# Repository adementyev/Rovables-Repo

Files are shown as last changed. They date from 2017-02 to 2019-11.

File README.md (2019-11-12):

# Rovables Project 

## Introduction
This repository has all the design files to assemble the robots. Rovables are miniature wearable robots that can move around the body. 
See the paper we published at UIST conference [here](http://www.artemdementyev.com/wp-content/uploads/2016/10/Rovables-Miniature-On-Body-Robots-as-Mobile-Wearables.pdf).  

Rovables rendered
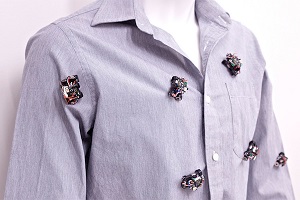
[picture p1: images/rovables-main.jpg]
Shirt pic


## Content
electronics/ - contains the circuit boards design. They were all designed using Altium, so it might be required to see the original files

mechanical/ - This folder contains mechanical files, done in SolidWorks 2016. 

software/ - contains the software that runs on the devices. We used the Arduino platform, so the robots can be easily programmed.  

## Manufacturing and design
The design contains many 3D printed custom parts and custom circuit boards. Making the design will require at least a good resolution 3D printer (Formlabs or Eden260). Other printers might work also, but we haven't tried them. 

## Known Issues
The same nRF42 library is used for the robot and the receiver. Change in nRF52.cpp file: #define TEENSY_MASTER_BOARD depending on which one, since they use different SPI port definitions. 

The localization of the robot is not implemented in the current code. This version has high resolution wheel encoders and a powerful ARM processor, so the tracking will be better. 

## Aknowledgements
This project was a collaboration between MIT Media Lab (Responsive Environments and Living Mobile) and Shape Lab at Stanford University

The poeple who worked on this project are:

Graduate students: Artem Dementyev, Hsin-Liu (Cindy) Kao, Inrak Choi, Deborah Ajilo, Maggie Xu. 

The faculty: Sean Follmer, Joe Paradiso, Chris Schmandt.

Undegraduate students: Lucas Santana, Karla-Sofia Zapata-Garcia, Cheyenne Hua, and Diana Lamaute

Shapelab Logo
MediaLab Logo

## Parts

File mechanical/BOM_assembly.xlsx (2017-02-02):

Part | Quantity | Supplier | Comments
Off Shelf
M2 7mm standoffs | 2 | Amazon (https://www.amazon.com/gp/product/B00W94LVRG/ref=oh_aui_detailpage_o06_s00?ie=UTF8&psc=1)
M2 4mm standoffs | 2 | Amazon (https://www.amazon.com/gp/product/B00R1IWHZU/ref=oh_aui_detailpage_o02_s00?ie=UTF8&psc=1)
M2 3mm screw | 6 | Amazon (https://www.amazon.com/gp/product/B00QFS2X2O/ref=oh_aui_detailpage_o00_s02?ie=UTF8&psc=1)
M1.6 3mm screw | 2 | Amazon (https://www.amazon.com/gp/product/B00QFSLIUM/ref=oh_aui_detailpage_o06_s00?ie=UTF8&psc=1)
M1.6 nut | 2 | Amazon (https://www.amazon.com/gp/product/B01LWZ5UXQ/ref=oh_aui_detailpage_o05_s00?ie=UTF8&psc=1)
Magnets | 4 | K&J Magnetics (https://www.kjmagnetics.com/search-pn.asp?pg=1&stext=R621) | 3/8'' x 1/8 '' x 1/16''
Thicker magnets | 2 | K&J Magnetics (https://www.kjmagnetics.com/proddetail.asp?prod=R622) | 3/8'' x 1/8'' x 1/8''
100mAh battery | 1 | Amazon (https://www.amazon.com/gp/product/B00IHA4W1S/ref=oh_aui_detailpage_o00_s00?ie=UTF8&psc=1)
4x8x3mm bearings | 2 | Amazon (https://www.amazon.com/gp/product/B019I2WVCA/ref=oh_aui_detailpage_o06_s00?ie=UTF8&psc=1)
Custom PCBs
Main control board | 1 | PCB cart (http://www.pcbcart.com/pcb-fab/pcb-prototype.html) | They can do 0.5mm 4-layer board
IR encoder boards | 2 | PCB cart (http://www.pcbcart.com/pcb-fab/pcb-prototype.html) | The board has to be routed correctly
Encoder disks | 2 | PCB cart (http://www.pcbcart.com/pcb-fab/pcb-prototype.html) | 0.5mm thick
Flex cables | 2 | King Credie (http://www.kingcredie.com/)
Programming shield | 1 | OSH park (https://oshpark.com/)
3D Printed
Main body | 1 | Formlabs | GPBK02 Resin, 25um resolution
undercarriage | 1 | Formlabs | GPBK02 Resin, 25um resolution
Ball bearing adapter | 2 | Formlabs | GPBK02 Resin, 25um resolution
Motor adapter | 2 | Formlabs | GPBK02 Resin, 25um resolution
Cover | 1 | Formlabs | GPBK02 Resin, 25um resolution
Rod for magnets | 1 | Formlabs | GPBK02 Resin, 25um resolution
Tools needed
#0 Phillips screwdriver | 1
Form 2 Printer | 1 |  | Eden260 is ok also
Solder iron | 1

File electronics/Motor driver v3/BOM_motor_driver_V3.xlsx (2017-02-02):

Comment | Description | Designator | Footprint | Quantity | Manufacturer 1 | Manufacturer Part Number 1 | Supplier 1 | Supplier Part Number 1
ON_OFF_SWITCH | SPDT SMD Side Switch | *1 | SWTICH_SMD_SIDE | 1 | Nidec / COPAL ELECTRONICS | CUS-12TB | Digi-Key | 563-1102-1-ND
2.4GHz SMT On-ground MID Chip Antenna | Bluetooth antenna | A1 | 47948-0001 | 1 | Molex | 479480001 | Digi-Key | WM4893CT-ND
2.45 GHz Bulan | for nRF8001 chip | B1 | 2450BM14A0002 | 1 | Johanson Technology | 2450BM14A0002T | Digi-Key | 712-1574-1-ND
100uF 6.3V | Polarised capacitor | C1 | CAP1206 | 1 | Vishay / Sprague | TL8A0107M6R3C | Digikey | 718-1920-1-ND
10uF 16V | Polarised capacitor | C2 | CAP0805 | 1 | Kyocera / AVX | F981C106MSA | Digi-Key | 478-8654-1-ND
10uF 6.3V | Polarised capacitor | C3 | 0805 TANTALUM | 1 | Kyocera / AVX | TPSR106K006R1000 | Digi-Key | 478-9265-1-ND
0.1uF | SMD Cap 1206 | C5, C12 | 0603W | 2 | Yageo | CC0603ZRY5V9BB104 | Digikey | 311-1343-1-ND
0.1uF | SMD Cap 1206 | C6, C10, C17, C18 | 0402 CAPACITOR | 4 | Samsung | CL05A104MP5NNNC | Digikey | 490-1318-1-ND
18pF | SMD Cap 1206 | C8, C9 | 0402 CAPACITOR | 2 | Murata | GRM1555C1H180JA01D | Digikey | 490-5858-1-ND
33nF X7R, +/- 10% | SMD Cap 1206 | C11 | 0402 CAPACITOR | 1 | Kemet | C0402C333K4RACTU | Digikey | 399-4891-1-ND
6pF NPO, +/- 2% | SMD Cap 1206 | C14, C15 | 0402 CAPACITOR | 2 | Murata | GRM1555C1H6R0WA01D | Digikey | 490-8223-1-ND
2200pF 5% | SMD Cap 1206 | C16, C19 | 0402 CAPACITOR | 2 | Kemet | C0402C222J3GACTU | Digikey | 399-8957-1-ND
10000pF | SMD Cap 1206 | C20 | 0402 CAPACITOR | 1 | Murata | GRM155R71H103KA88D | Digikey | 490-4516-1-ND
10uF 16V | SMD Cap 1206 | C22 | 0603W | 1 | Murata (https://octopart-clicks.com/click/altium?sku=81-GRM188C81C106MA3D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) | GRM188R60G106ME47D (https://octopart-clicks.com/click/altium?sku=81-GRM188C81C106MA3D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) | Digikey | 490-3298-1-ND (https://octopart-clicks.com/click/altium?sku=81-GRM188C81C106MA3D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)
4.7uF 10V | SMD Cap 1206 | C23 | 0603W | 1 | Murata | GRM188R61A475KE15D | Digikey | 490-10477-1-ND
Ferrite bead |  | L1 | 0603W | 1 | Murata | BLM18PG471SN1D | Digikey | 490-5223-1-ND
LED BLUE | LED SMD 1206/0603 | LED1 | 0402W | 1 | Panasonic / Panasonic SSG | LNJ947W8CRA | Digi-Key | LNJ947W8CRACT-ND
LED RED | LED SMD 1206/0603 | LED2 | 0402W | 1 | Panasonic / Panasonic SSG | LNJ247W82RA | Digi-Key | LNJ247W82RACT-ND
LED ORANGE | LED SMD 1206/0603 | LED3 | 0402W | 1 | Panasonic / Panasonic SSG | LNJ437W84RA | Digi-Key | LNJ437W84RACT-ND
32.768 kHz |  | O1 | 32.768 Crystal | 1 | ECS International | ECS-.327-12.5-34B-TR | Digi-Key | XC1617CT-ND
16 MHz Crystal Cl=8pF | For BLE use | O2 | 2.5 x 2.0 crystal | 1 | Nihon Dempa Kogyo (NDK) | NX2520SA-16MHZ-STD-CSW-5 | Digi-Key | 644-1169-1-ND
FH33J-4S-0.5SH(99) | 0.5mm FPC connector | P3, P5, P6 | FH33J-4S-0.5SH(99) | 3 | Hirose Electric (HRS) | FH33J-4S-0.5SH(99) | Digi-Key | H124646CT-ND
CONN HEADER 20POS |  | P4 | DF12 20 POS | 1 | Hirose Electric (HRS) | DF12D(4.0)-20DP-0.5V(81) | Digi-Key | H11743CT-ND
10K |  | R2 | 0402 RESISTOR | 1 | Yageo | RC0402JR-0710KL | Digikey | 311-10KJRCT-ND
0 Ohm |  | R3, R4, R5 | 0402 RESISTOR | 3 | Yageo | RC0603JR-070RL | Digikey | 311-0.0GRCT-ND
22K 1% |  | R6 | 0402 RESISTOR | 1 | Yageo | RC0402FR-0722KL | Digikey | 311-22.0KLRCT-ND
330 |  | R7, R8 | 0402 RESISTOR | 2 | Yageo | RC0402JR-07330RL | Digikey | 311-330JRCT-ND
49.9K |  | R10, R13 | 0603W | 2 | Yageo | RC0603FR-0749K9L | Digikey | 311-49.9KHRCT-ND
20K |  | R11, R14 | 0603W | 2 | Yageo | RC0603FR-0720KL | Digikey | 311-20.0KHRCT-ND
200K |  | R12, R15 | 0603W | 2 | Yageo | RC0603FR-07200KL | Digikey | 311-200KHRCT-ND
4.7K 5% |  | R16, R17 | 0402 RESISTOR | 2 | Yageo | RC0402JR-074K7L | Digikey | 311-4.7KJRCT-ND
4.99K 1% |  | R18 | 0603W | 1 | Panasonic / Panasonic ECG | ERJ-3EKF4991V | Digikey | P4.99KHCT-ND
1K 5% |  | R20 | 0603W | 1 | Yageo | RC0603JR-071KL | Digikey | 311-1.0KGRCT-ND
3.3V REG | 5V LDO SMD | U1 | SOT-23-5 | 1 | Microchip Technology (https://octopart-clicks.com/click/altium?manufacturer=Microchip%20%2F%20Micrel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) | MIC5219-5.0YM5-TR (https://octopart-clicks.com/click/altium?manufacturer=Microchip%20%2F%20Micrel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) | Digi-Key | 576-1281-1-ND
3.3 V REG | 5V LDO SMD | U2 | SOT-23-5 | 1 | Microchip Technology (https://octopart-clicks.com/click/altium?manufacturer=Microchip%20Technology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) | MIC5205-3.3YM5-TR (https://octopart-clicks.com/click/altium?manufacturer=Microchip%20Technology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) | Digi-Key | 576-1259-1-ND (https://octopart-clicks.com/click/altium?manufacturer=Microchip%20Technology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)
MCP73831T |  | U4 | SOT-23-5 | 1 | Microchip Technology | MCP73831T-2ACI/OT | Digi-Key | MCP73831T-2ACI/OTCT-ND
nRF24L01+ | 2.4 GHz Radio | U6 | QFN20 | 1 | Nordic Semiconductor | nRF24L01P-R7 | Digi-Key | 1490-1033-1-ND
DRV8835 |  | U8 | WSON-16 | 1 | Texas Instruments (TI) | DRV8835DSSR | Digi-Key | 296-30391-1-ND
MPU 6050 | Gyro / accelerometer combo | U9 | QFN24 | 1 | Invensense | MPU-6050 | Digi-Key | 1428-1007-1-ND
MCP6422 | 4.4 µA/Amplifier, 90 kHz Op Amp | U10 | MSOP-MS8_N | 1 | Microchip Technology | MCP6422-E/MS | Digi-Key | MCP6422-E/MS-ND
ATSAMD21G | IC MCU 32BIT 256KB FLASH 48TQFP | U*1 | TQFN48 | 1 | Atmel | ATSAMD21G18A-AUT | Digi-Key | ATSAMD21G18A-AUTCT-ND

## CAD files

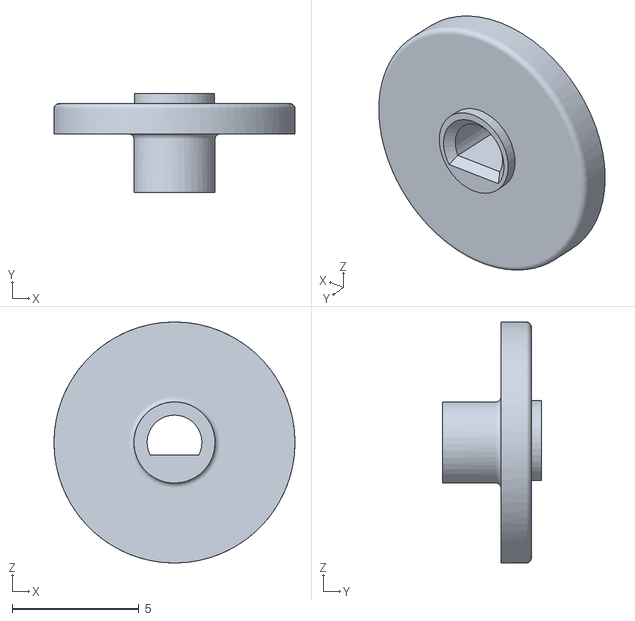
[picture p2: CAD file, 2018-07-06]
mechanical/CAD Robot/Rovables_assembly_magnetic_v5_for_3D_print/Mt_Mg Adapter V2.STL
9.50 x 3.90 x 9.50

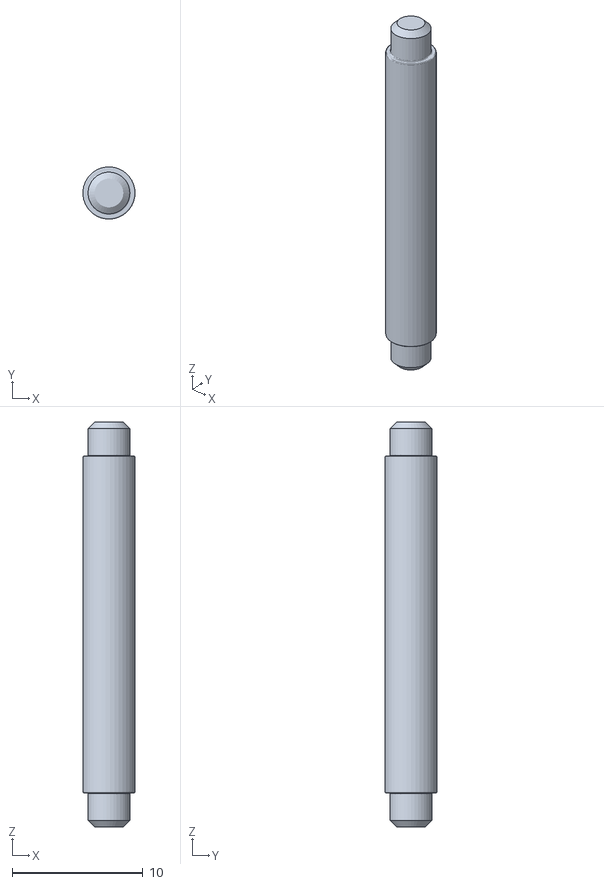
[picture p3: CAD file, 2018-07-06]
mechanical/CAD Robot/Rovables_assembly_magnetic_v5_for_3D_print/Magnet Holder V1C.STL
3.99 x 4.00 x 31.0

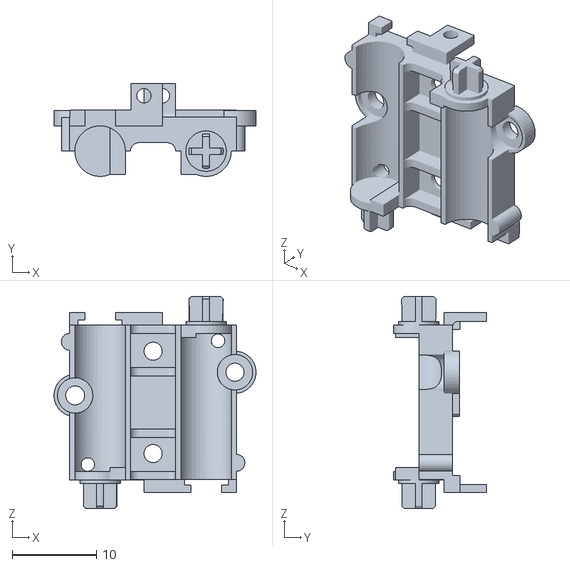
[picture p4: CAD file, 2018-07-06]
mechanical/CAD Robot/Rovables_assembly_magnetic_v5_for_3D_print/base_plate_v1.STL
23.9 x 11.0 x 25.2

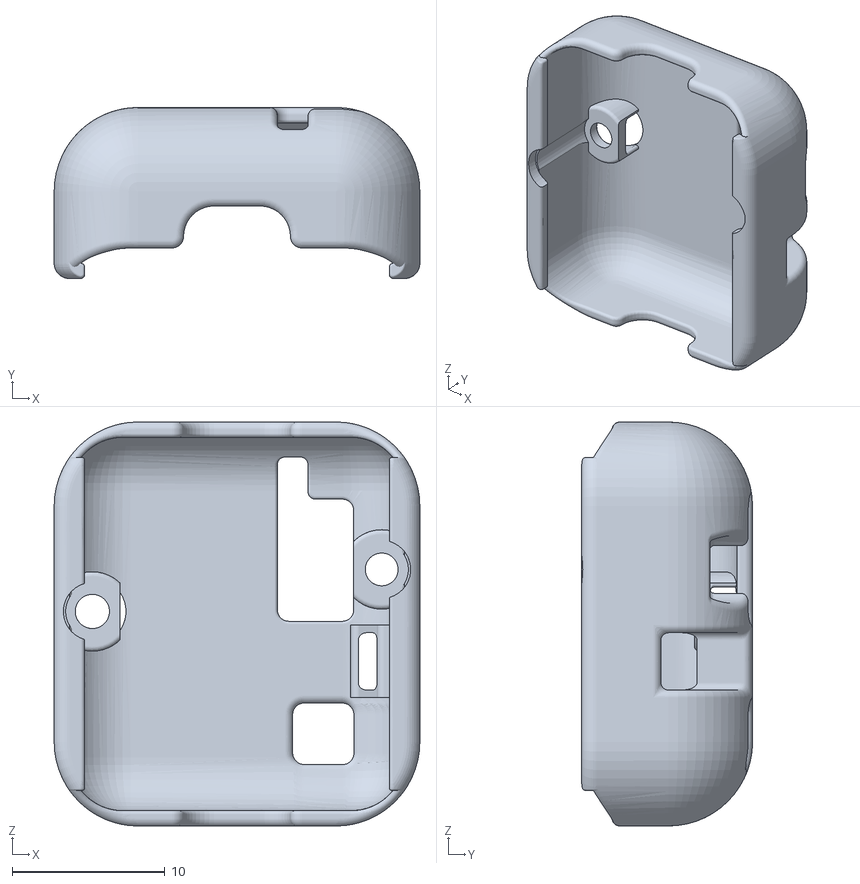
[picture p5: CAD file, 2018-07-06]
mechanical/CAD Robot/Rovables_assembly_magnetic_v5_for_3D_print/case_minimum_covered.STL
24.0 x 11.2 x 26.5

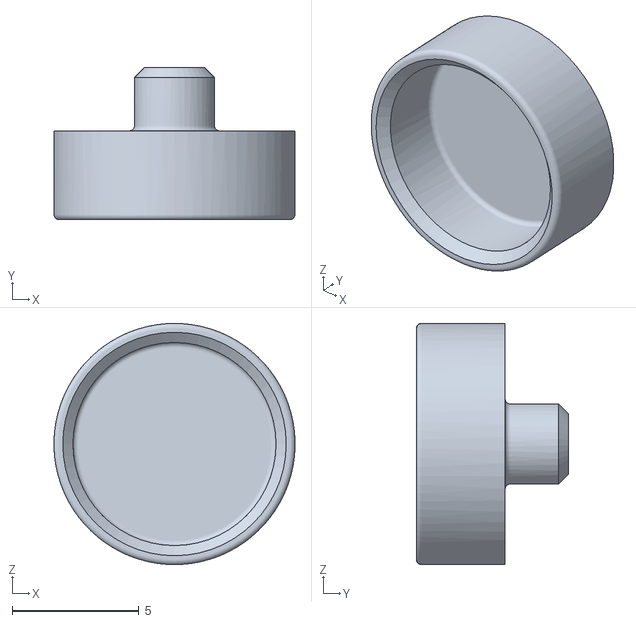
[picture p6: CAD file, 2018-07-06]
mechanical/CAD Robot/Rovables_assembly_magnetic_v5_for_3D_print/BB_Mg Adapter V2.STL
9.49 x 6.00 x 9.50

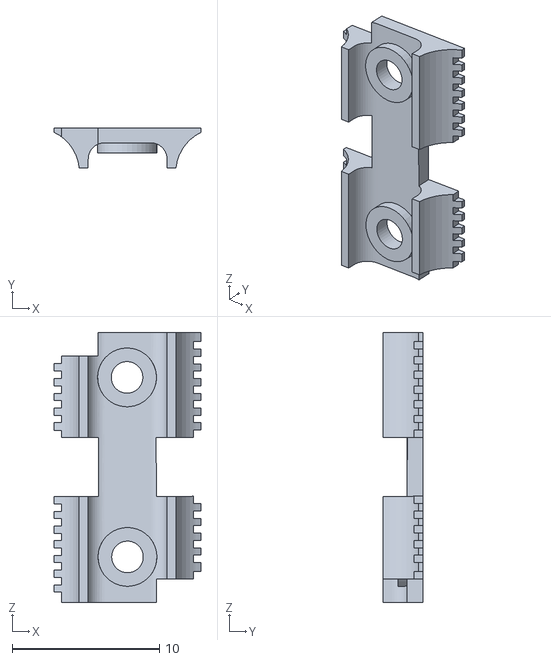
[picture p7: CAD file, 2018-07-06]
mechanical/CAD Robot/Rovables_assembly_magnetic_v5_for_3D_print/bottom_ski_v1.STL
9.99 x 2.70 x 18.4

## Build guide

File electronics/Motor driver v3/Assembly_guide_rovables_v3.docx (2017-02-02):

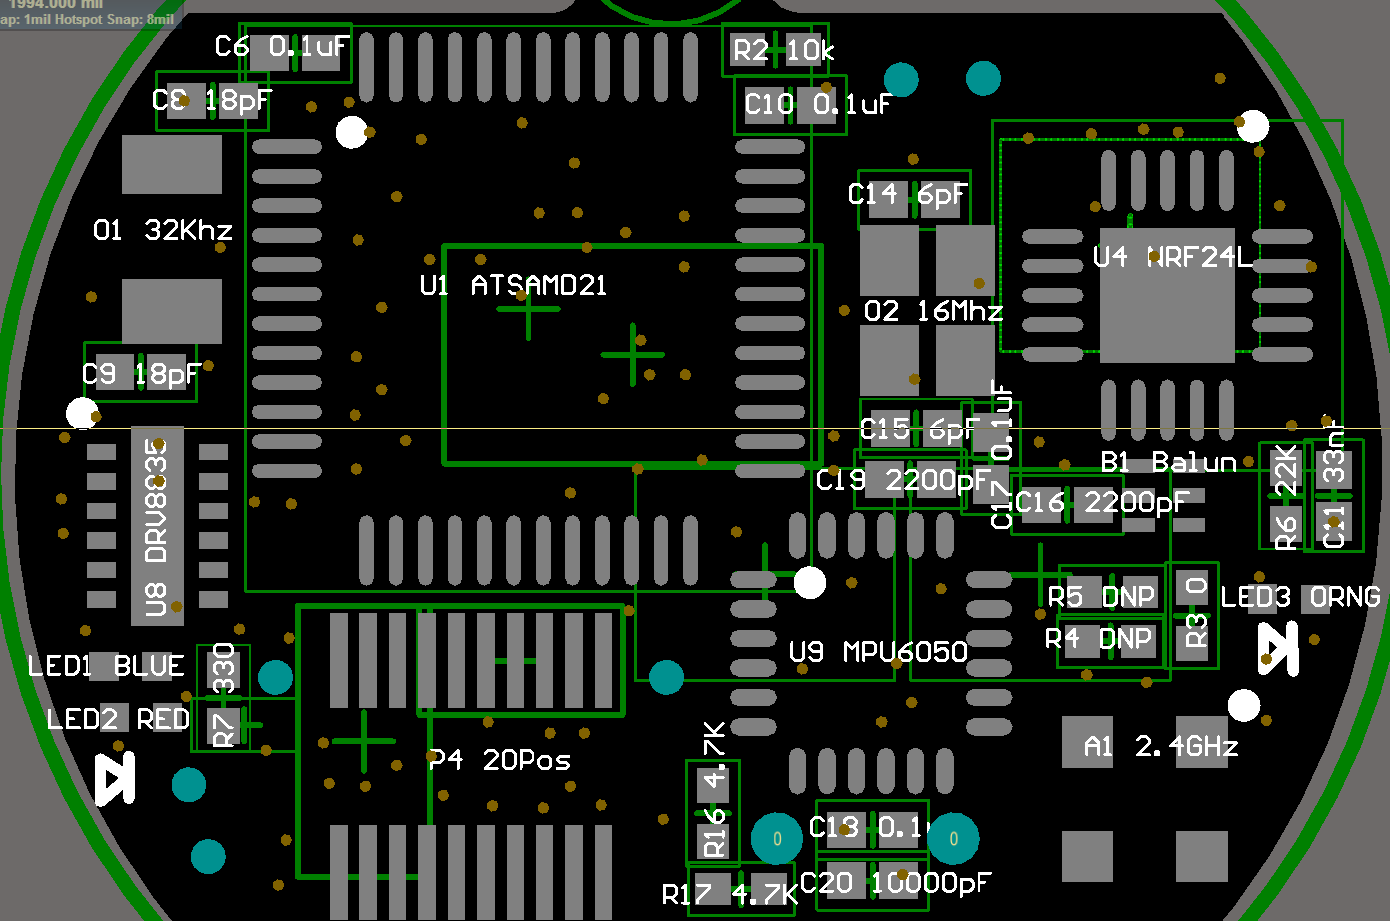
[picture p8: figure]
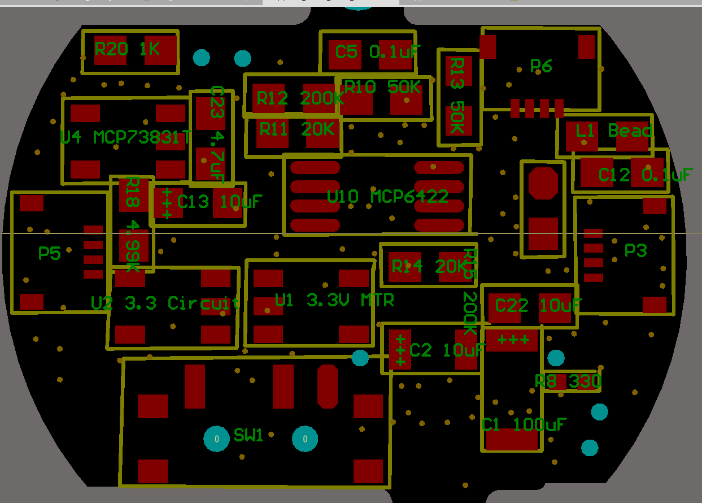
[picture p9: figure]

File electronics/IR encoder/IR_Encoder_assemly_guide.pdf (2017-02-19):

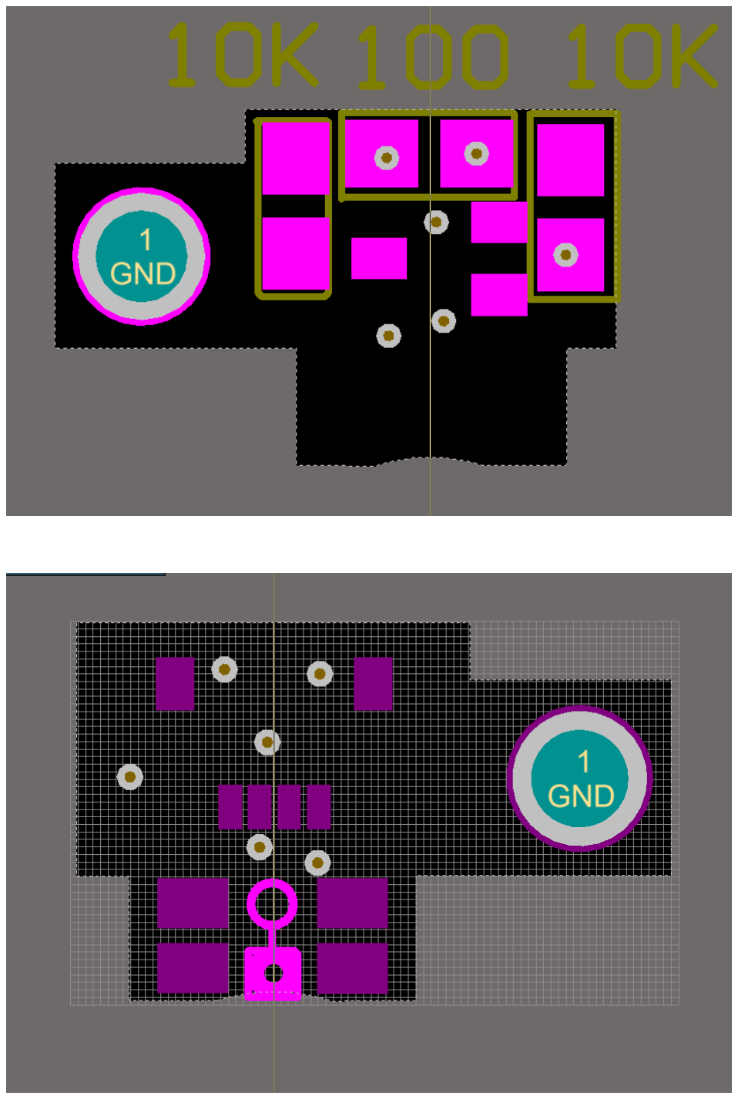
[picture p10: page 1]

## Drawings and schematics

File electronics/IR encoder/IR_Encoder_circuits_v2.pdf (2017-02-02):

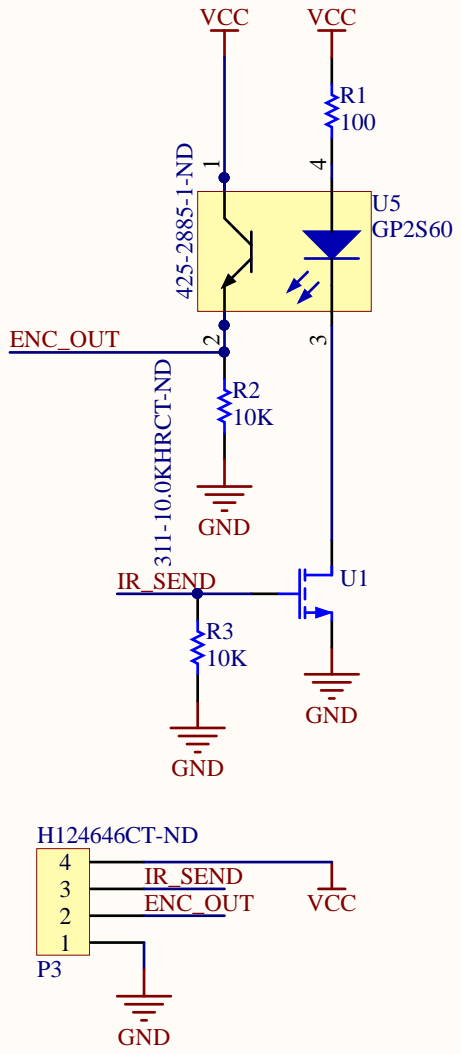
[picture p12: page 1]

IR Encoder Board Title

Designed by Artem Dementyev | 2 Ver

Date: 2/2/2017 Time: 2:40:27 PM

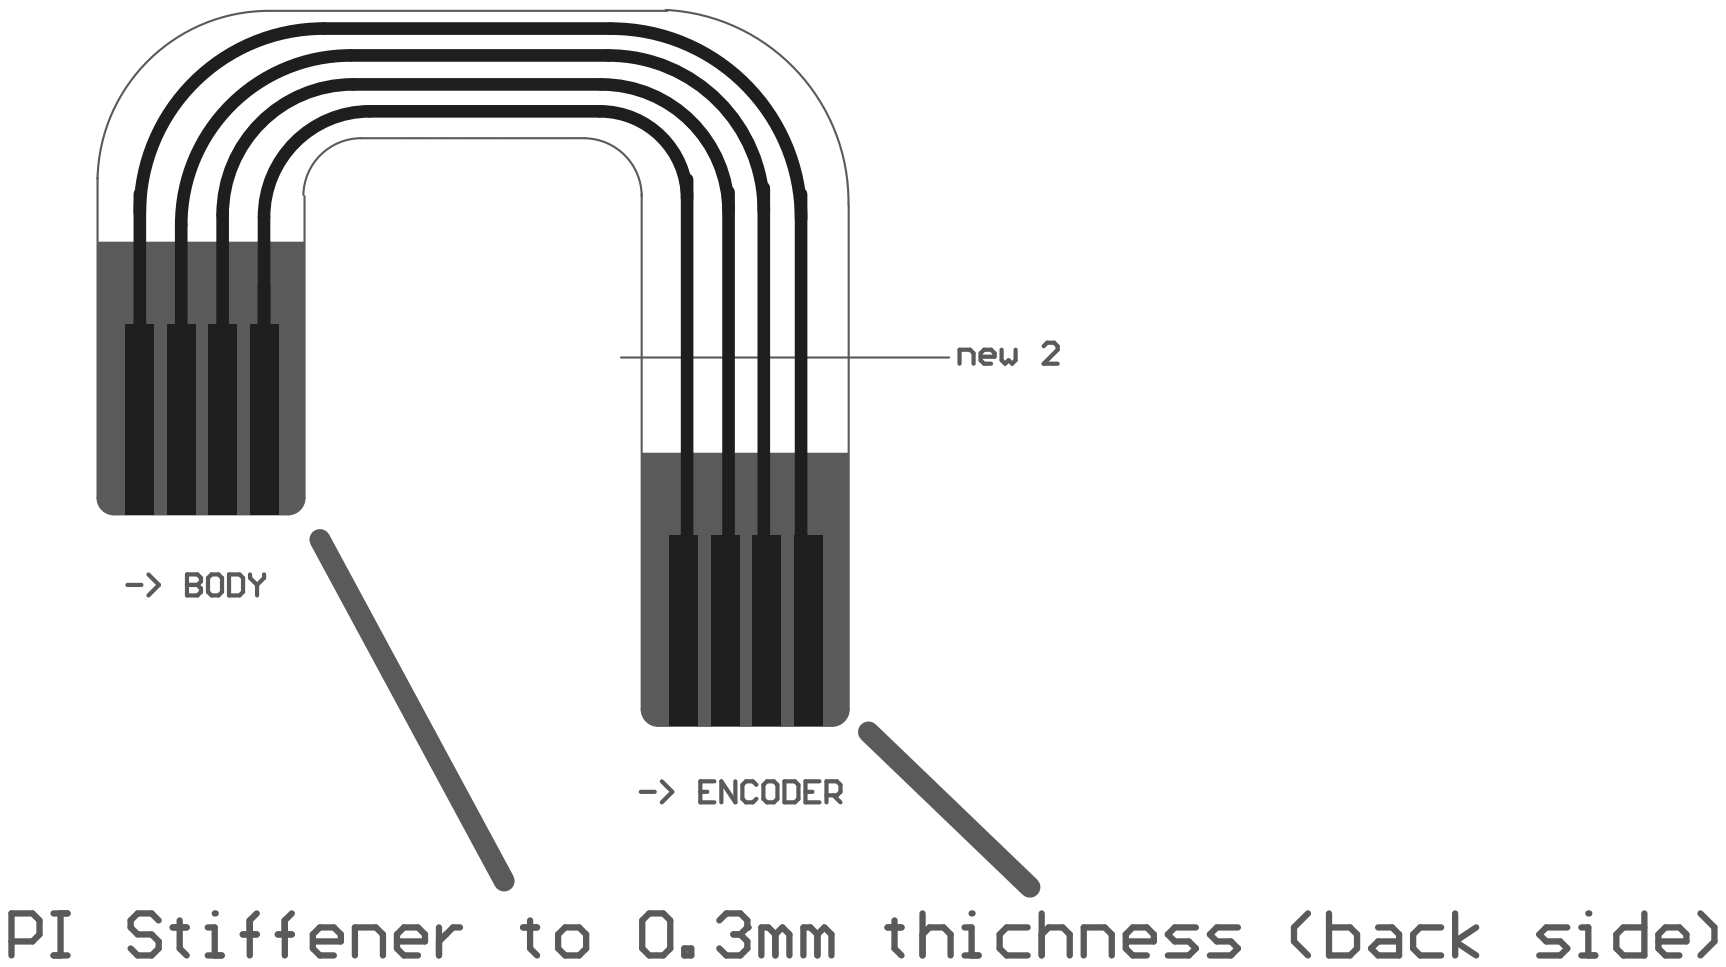
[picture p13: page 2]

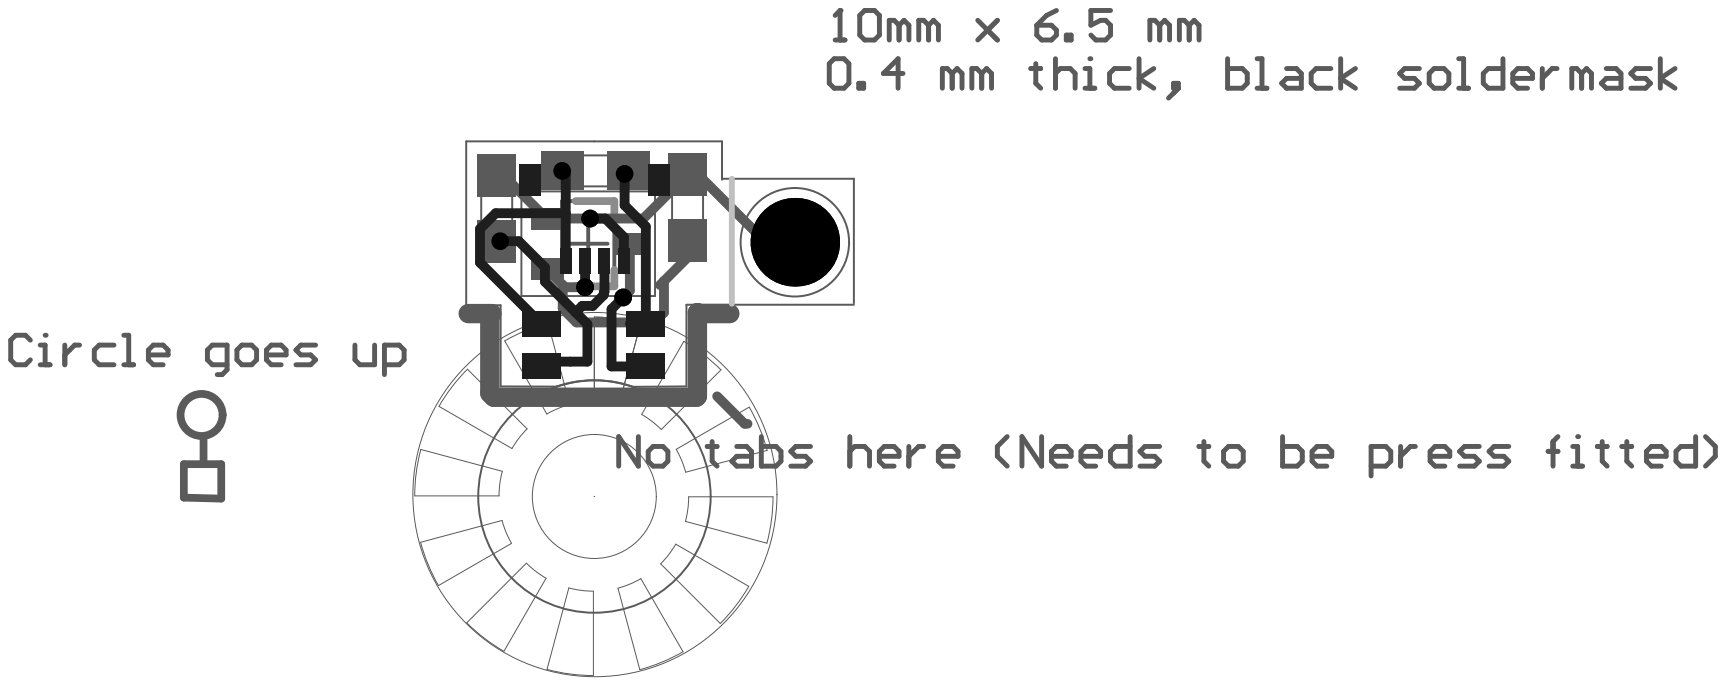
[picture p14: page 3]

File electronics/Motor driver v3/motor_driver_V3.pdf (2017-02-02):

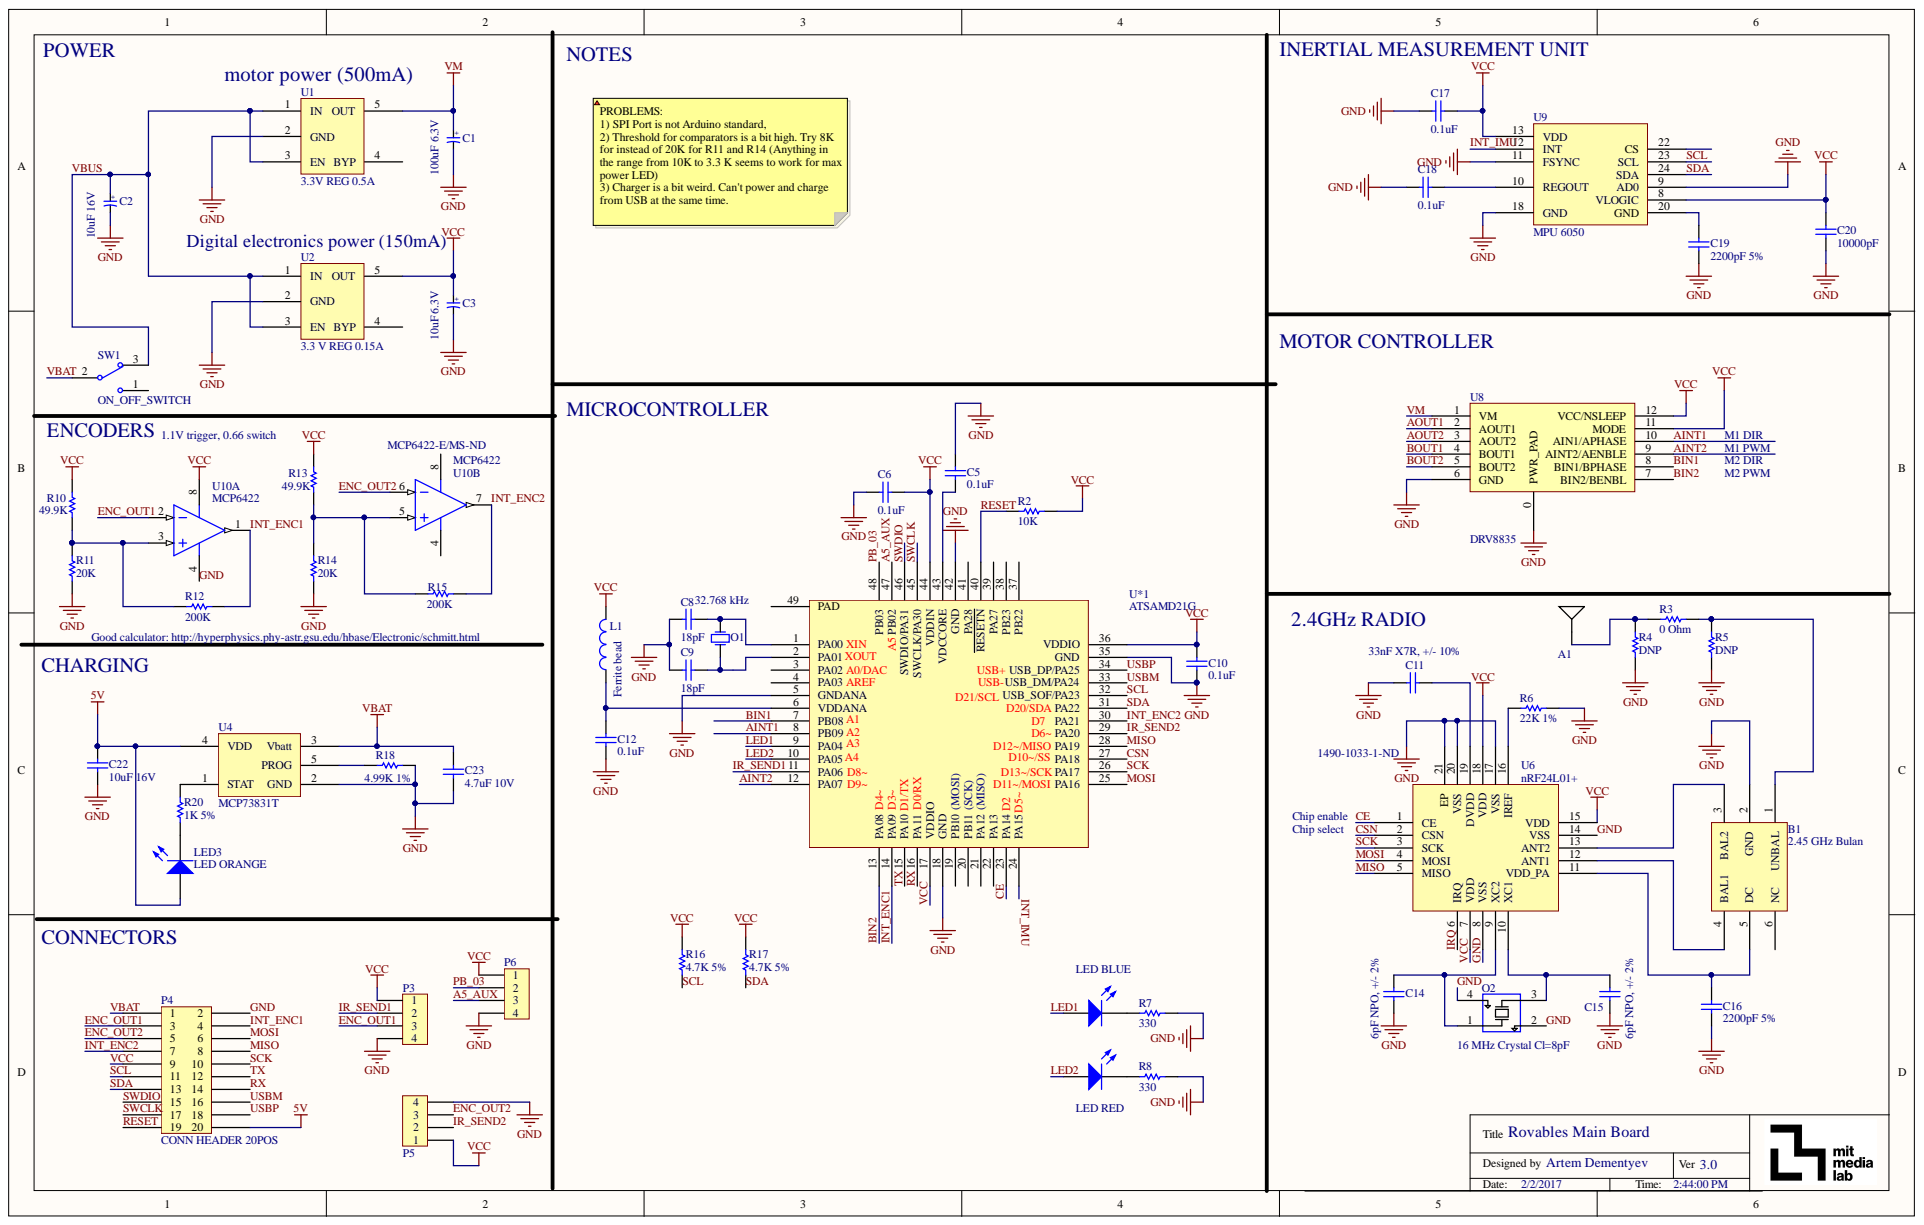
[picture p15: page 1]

tead of 20K for R
the range from 10K to 3.3 K seem
power L

Anything in
s to work for max

3) Charger i
from USB at the same t

tr.gsu.edu/hbase/E

IREF 16 VSS 17 VDD 18 DVDD 19 VSS 20 V

Des igned by A r tem Demen t yev | 3 . 0 Ver

Date: 2/2/2017 | Ti me: 2:44:00 PM

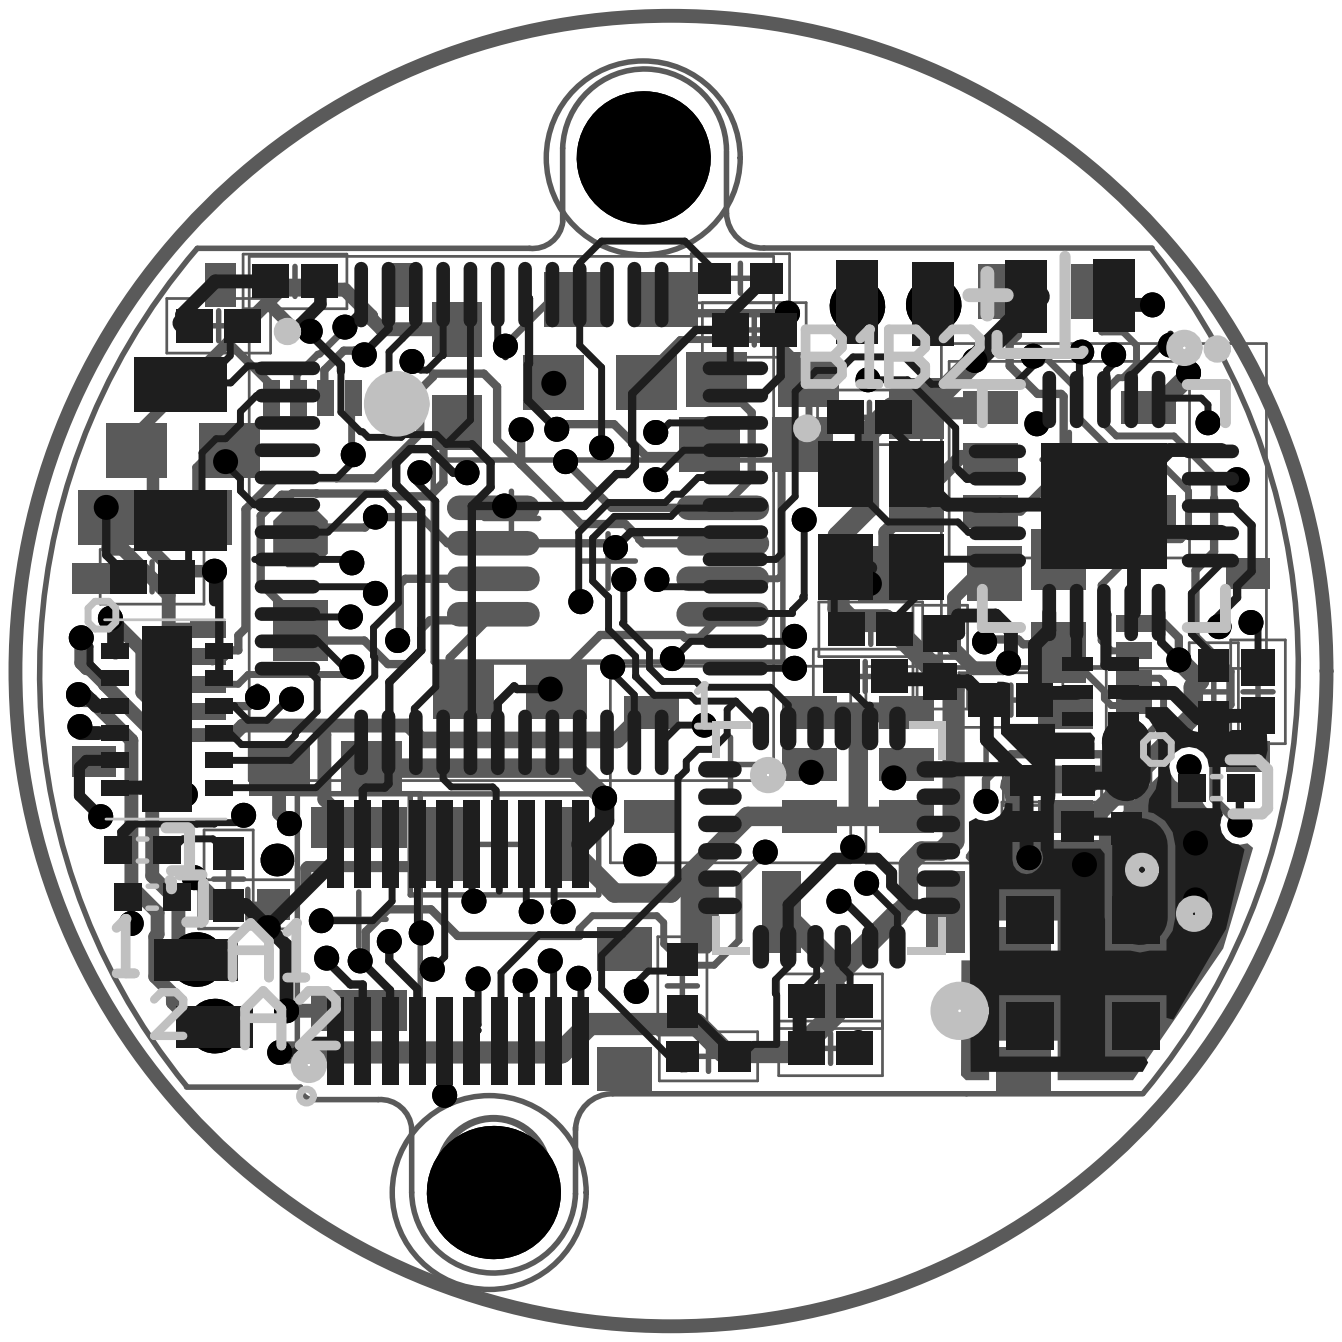
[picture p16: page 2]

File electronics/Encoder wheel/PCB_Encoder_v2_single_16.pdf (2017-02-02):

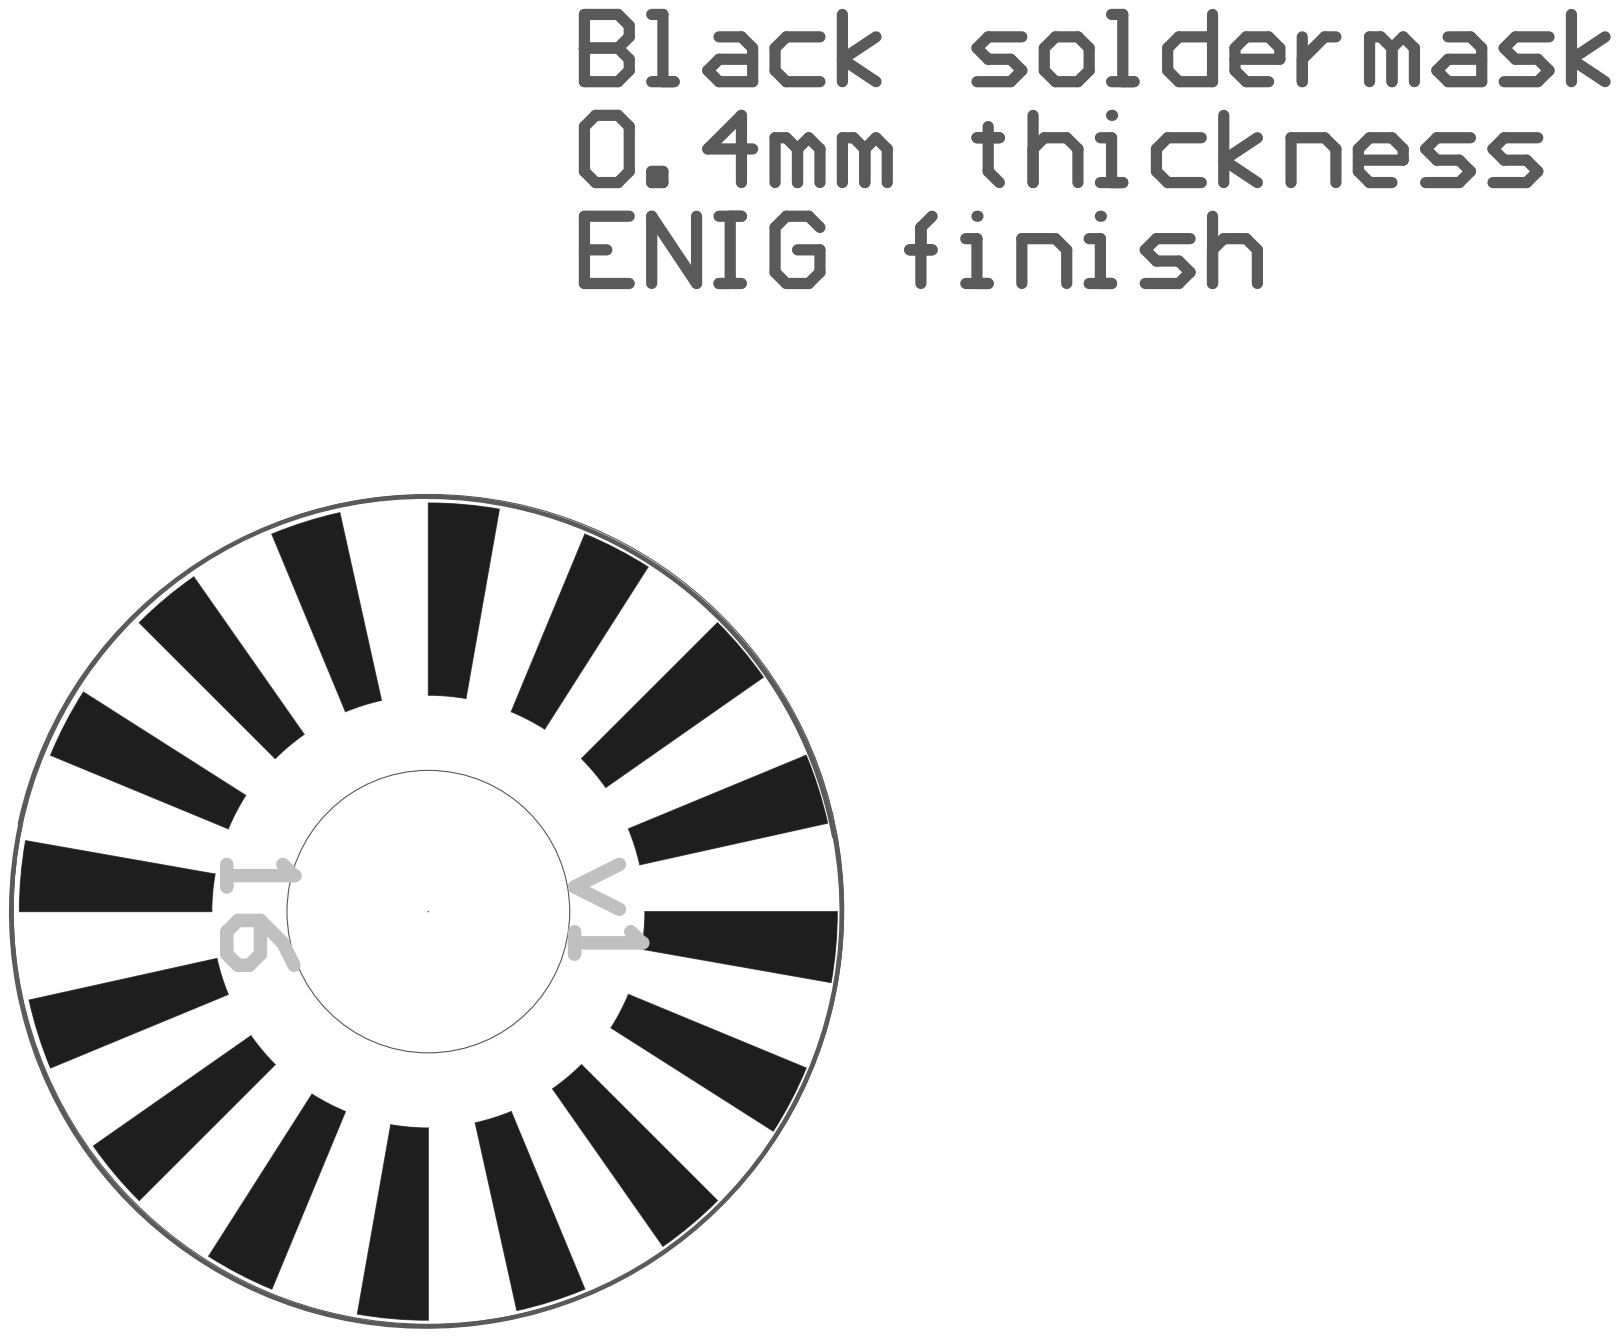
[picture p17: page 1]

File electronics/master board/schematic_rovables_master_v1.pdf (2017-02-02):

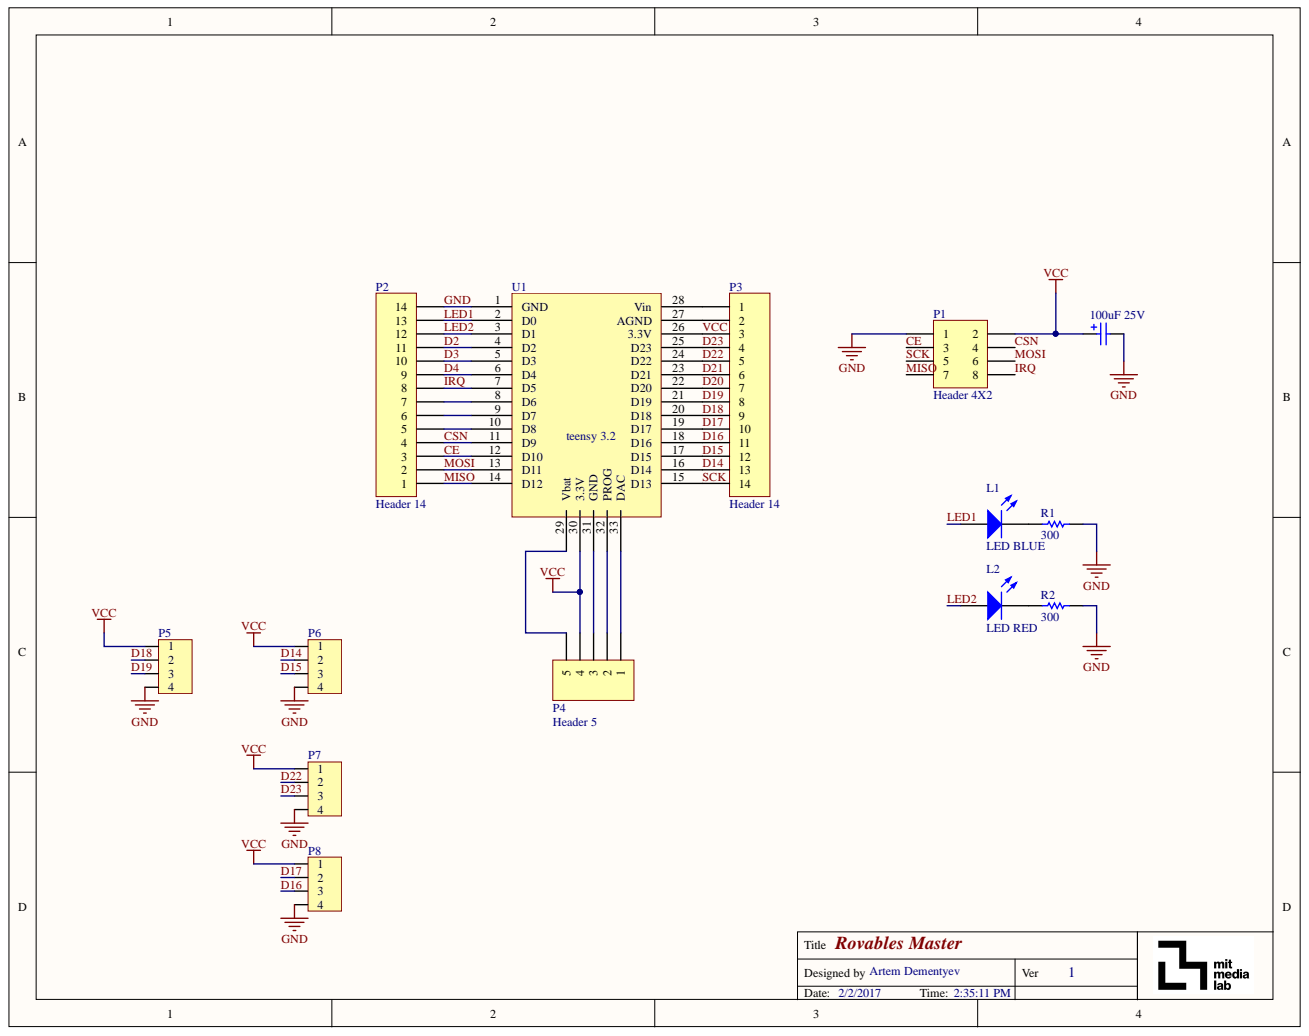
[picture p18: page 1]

D4 | D4 6 | D21
IRQ | D5 7 | D20

D6 8 | D19
D7 9 | D18
D8 10 | D17

CSN | D9 11 | D16
CE | D10 12 | D15
MOSI | D11 13 | D14
MISO | | SCK

Rovables Master Title

Designed by Artem Dementyev | 1 Ver

Date: 2/2/2017 Time: 2:35:11 PM

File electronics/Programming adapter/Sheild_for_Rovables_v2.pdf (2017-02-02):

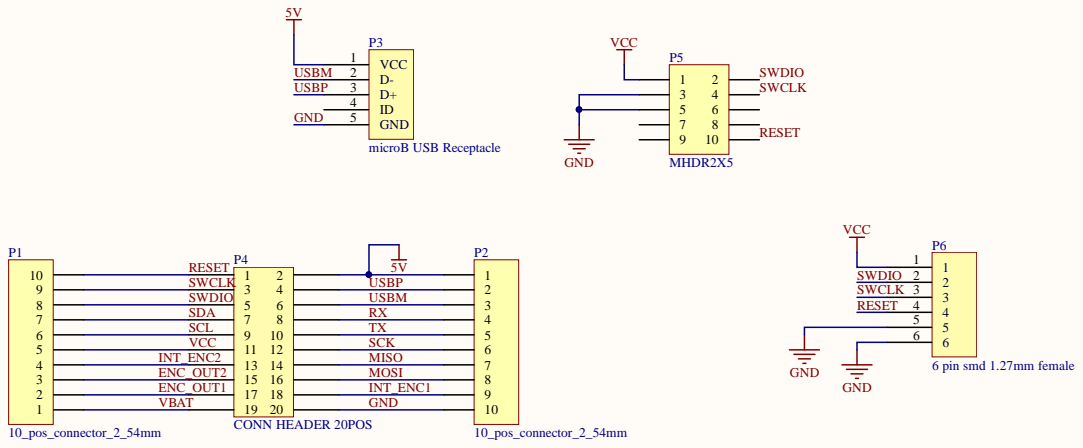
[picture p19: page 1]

S WCL K | U SBP
S W DIO | SBM

IN T_E NC2 | MIS O
E NC_O U T 2 | S I
E NC_O U T 1 | IN T_E NC1
VBAT | G N D

ramming Adap ter Shield Ti t l e Pr o g

Art e m D e m entye v D e s igned by | 2 Ve r

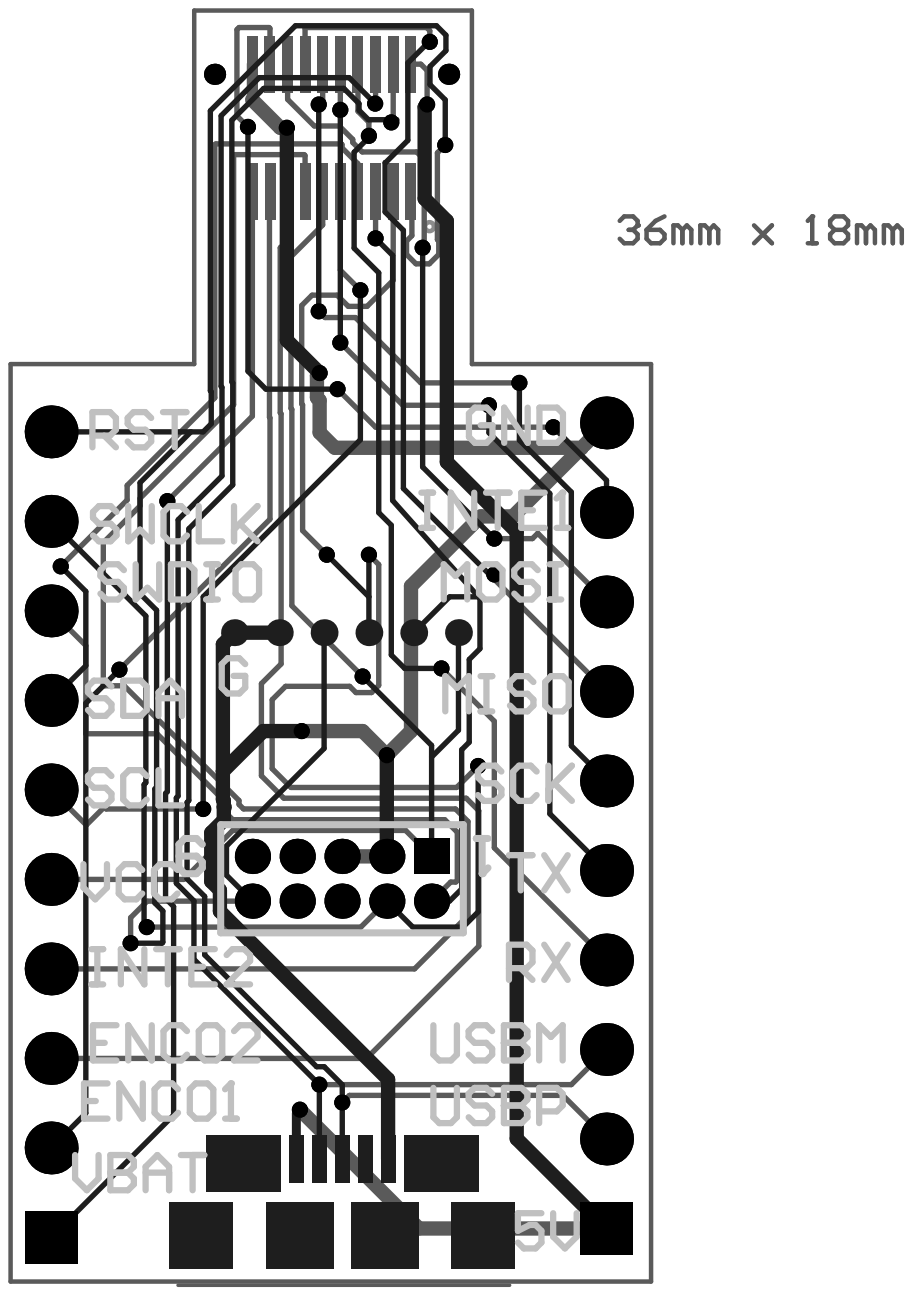
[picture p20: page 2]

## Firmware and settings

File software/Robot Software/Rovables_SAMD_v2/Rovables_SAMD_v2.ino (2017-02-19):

//TODO: Add radio powerdown/up

#include <SPI.h>
#include "nRF24L01.h"
#include "RF24.h"
#include<Wire.h>
#include "definitions.h"


RF24 radio(CE,CSN); // Default SPI speed is 4Mbit, but should work up to 10MBbit

#define WHICH_NODE 4     // must be a number from 0 - 5 identifying the PTX node 

const uint64_t pipes[] =  {0x7878787878LL, 0xB3B4B5B6F1LL, 0xB3B4B5B6CDLL, 0xB3B4B5B6A3LL, 0xB3B4B5B60FLL, 0xB3B4B5B605LL};
const uint64_t PTXpipe = pipes[ WHICH_NODE ];   // Pulls the address from the above array for this node's pipe

uint8_t dataToWrite[] = {1,1,1,1,1,1};
uint8_t receiveData[PACKET_SIZE];
bool SERIAL_DEBUG  = false;

byte counter = 0;
byte failureToWriteCounter =0;

int testCount=0;
bool ledState = 0;

int16_t AcX,AcY,AcZ,Tmp,GyX,GyY,GyZ; 

bool timer4Interrupt = false;
int xPos = 0;
int yPos = 0; 

uint8_t encoder1Counter = 0 ;
uint8_t encoder2Counter = 0 ;

void setup(void)
{
  pinMode(LED_BLUE, OUTPUT); 
  pinMode(LED_RED, OUTPUT);
  pinMode(M1_DIR, OUTPUT); 
  pinMode(M1_PWM, OUTPUT); 
  pinMode(M2_PWM, OUTPUT); 
  pinMode(M2_DIR, OUTPUT); 
  pinMode(TX_PIN, OUTPUT);
  pinMode(INT_IMU, INPUT);
  pinMode(ENC1_INT, INPUT); 
  pinMode(ENC2_INT, INPUT); 
  pinMode(ENC1_LED, OUTPUT); 
  pinMode(ENC2_LED, OUTPUT);

  turnOnEncoders();

  if(SERIAL_DEBUG) SerialUSB.begin(0);

  radio.begin();

  radio.setRetries(10,0); //retries, delay
  radio.setPayloadSize(PACKET_SIZE);
  radio.setDataRate(RF24_2MBPS);
  radio.setChannel(60);

  radio.openReadingPipe(0,PTXpipe);  //open reading or receive pipe
  radio.stopListening();

  //Flash LEDs to undicate startup
  for(int i=0; i<5; i++) {
    digitalWrite(LED_RED, HIGH); 
    digitalWrite(LED_BLUE, LOW); 
    delay(100);
    digitalWrite(LED_RED, LOW); 
    digitalWrite(LED_BLUE, HIGH); 
    delay(100);
  }
    digitalWrite(LED_BLUE, LOW); 

  //Start the interrupt routines
  attachInterrupt(ENC1_INT, ENC1_INT_Routine, FALLING); 
  attachInterrupt(ENC2_INT, ENC2_INT_Routine, FALLING);
  startTransmitTimer4(10);//freq in Hz
}

//----------------MAIN LOOP-----------------
void loop(void)
{
  
  if(timer4Interrupt==true) { 
    dataToWrite[1] = counter;
    dataToWrite[2] =failureToWriteCounter;
    dataToWrite[3] = encoder1Counter;  
    dataToWrite[4] = encoder2Counter;
    sendAndReceiveResponse();
    timer4Interrupt=false;

  } 
}

//------------HANDLE TIMER 4 INTERRUPT---------------
void TC4_Handler()   
{     
  // Check for overflow (OVF) interrupt
  if (TC4->COUNT16.INTFLAG.bit.OVF && TC4->COUNT16.INTENSET.bit.OVF)             
  {
    timer4Interrupt = true;
    counter++;
    REG_TC4_INTFLAG = TC_INTFLAG_OVF;         // Clear the OVF interrupt flag
  }
}

//------------HANDLE ENCODER INTERRUPTS---------------
void ENC1_INT_Routine() { 
 encoder1Counter++; 
}
void ENC2_INT_Routine() { 
  encoder2Counter++;
}

void sendAndReceiveResponse() { 
  radio.powerUp();
  //Send radio data  
  radio.stopListening();
  radio.openWritingPipe(PTXpipe);        //open writing or transmit pipe
  if (!radio.write( &dataToWrite, PACKET_SIZE )){  //if the write fails let the user know over serial monitor
     if(SERIAL_DEBUG)SerialUSB.println("Failed");   
     failureToWriteCounter++;   
  } 
 else {
    if(SERIAL_DEBUG)SerialUSB.println("SUCCESS");
  }

  //wait for a reply
  radio.startListening();  
  unsigned long started_waiting_at = millis();
  bool timeout = false;
    while ( ! radio.available() && ! timeout )
      if (millis() - started_waiting_at > 50 )
        timeout = true;
    if ( timeout )
    {
      if(SERIAL_DEBUG)SerialUSB.println("Failed, response timed out.\n\r");
      //timeOutCount++;
    }
    else
    {
      radio.read( &receiveData, PACKET_SIZE );
         toogleLedWhenData();
        switch(receiveData[0]) { 
          case 0x00: 
          break; 
          case IGNORE: 
          break; 
          case MOTOR_CRL: 
             analogWrite(M1_PWM, receiveData[1]);
             analogWrite(M2_PWM, receiveData[2]);
             digitalWrite(M1_DIR, receiveData[3]); 
             digitalWrite(M2_DIR, receiveData[4]);
          break;
          case 0x03:       
          break;
        }
    }
    radio.powerDown();
}

void toogleLedWhenData() {
  testCount++;
  if (testCount>5) { 
    if(ledState == 0) { 
      digitalWrite(LED_BLUE, HIGH);
      ledState=1;
      testCount=0;
  }
  else if (ledState == 1) {
      digitalWrite(LED_BLUE, LOW);
      ledState=0;
      testCount=0;
    }
  }
}

void getDataFromMPU6050() { 
  Wire.beginTransmission(MPU_ADDRESS);
  Wire.write(0x3B);  // starting with register 0x3B (ACCEL_XOUT_H)
  Wire.endTransmission(false);
  Wire.requestFrom(MPU_ADDRESS,14,true);  // request a total of 14 registers
  AcX=Wire.read()<<8|Wire.read();  // 0x3B (ACCEL_XOUT_H) & 0x3C (ACCEL_XOUT_L)    
  AcY=Wire.read()<<8|Wire.read();  // 0x3D (ACCEL_YOUT_H) & 0x3E (ACCEL_YOUT_L)
  AcZ=Wire.read()<<8|Wire.read();  // 0x3F (ACCEL_ZOUT_H) & 0x40 (ACCEL_ZOUT_L)
  Tmp=Wire.read()<<8|Wire.read();  // 0x41 (TEMP_OUT_H) & 0x42 (TEMP_OUT_L)
  GyX=Wire.read()<<8|Wire.read();  // 0x43 (GYRO_XOUT_H) & 0x44 (GYRO_XOUT_L)
  GyY=Wire.read()<<8|Wire.read();  // 0x45 (GYRO_YOUT_H) & 0x46 (GYRO_YOUT_L)
  GyZ=Wire.read()<<8|Wire.read();  // 0x47 (GYRO_ZOUT_H) & 0x48 (GYRO_ZOUT_L)
}

void serialDebugMPU6050() { 
 SerialUSB.print("$");
  SerialUSB.print(",");
  SerialUSB.print(AcX);
  SerialUSB.print(","); 
  SerialUSB.print(AcY);
  SerialUSB.print(",");
  SerialUSB.print(AcZ);
  SerialUSB.print(","); 
  SerialUSB.print(GyX);
  SerialUSB.print(","); 
  SerialUSB.print(GyY);
  SerialUSB.print(","); 
  SerialUSB.print(GyZ);
  SerialUSB.print(","); 
  SerialUSB.print(millis());
  SerialUSB.print(",");
  SerialUSB.println(Tmp/340.00+36.53);  //equation for temperature in degrees C from datasheet 
}

void startI2C_400KHz() { 
  Wire.begin();   
  sercom3.disableWIRE();   
  SERCOM3->I2CM.BAUD.bit.BAUD = SystemCoreClock / ( 2 * 400000) - 1 ; 
  sercom3.enableWIRE();    
}

void startTransmitTimer4(int freq) {
  // Set up the generic clock (GCLK4) used to clock timers
  REG_GCLK_GENDIV = GCLK_GENDIV_DIV(1) |          // Divide the 48MHz clock source by divisor 1: 48MHz/1=48MHz
                    GCLK_GENDIV_ID(4);            // Select Generic Clock (GCLK) 4
  while (GCLK->STATUS.bit.SYNCBUSY);              // Wait for synchronization

  REG_GCLK_GENCTRL = GCLK_GENCTRL_IDC |           // Set the duty cycle to 50/50 HIGH/LOW
                     GCLK_GENCTRL_GENEN |         // Enable GCLK4
                     GCLK_GENCTRL_SRC_DFLL48M |   // Set the 48MHz clock source
                     GCLK_GENCTRL_ID(4);          // Select GCLK4
  while (GCLK->STATUS.bit.SYNCBUSY);              // Wait for synchronization

  // Feed GCLK4 to TC4 and TC5
  REG_GCLK_CLKCTRL = GCLK_CLKCTRL_CLKEN |         // Enable GCLK4 to TC4 and TC5
                     GCLK_CLKCTRL_GEN_GCLK4 |     // Select GCLK4
                     GCLK_CLKCTRL_ID_TC4_TC5;     // Feed the GCLK4 to TC4 and TC5
  while (GCLK->STATUS.bit.SYNCBUSY);              // Wait for synchronization

  REG_TC4_COUNT16_CC0 = 48000000/(freq*256) -1;
  //REG_TC4_COUNT16_CC0 = 9374;                   // Set the TC4 CC0 register as the TOP value in match frequency mode
  //REG_TC4_COUNT16_CC0 = 0xB71A;                   // Set the TC4 CC0 register as the TOP value in match frequency mode
  //Freq(HZ) = 48000000/(PRESCALE*(CCO_REG+1))
  //9374  - 20 Hz
  
  while (TC4->COUNT16.STATUS.bit.SYNCBUSY);       // Wait for synchronization

  //NVIC_DisableIRQ(TC4_IRQn);
  //NVIC_ClearPendingIRQ(TC4_IRQn);
  NVIC_SetPriority(TC4_IRQn, 0);    // Set the Nested Vector Interrupt Controller (NVIC) priority for TC4 to 0 (highest)
  NVIC_EnableIRQ(TC4_IRQn);         // Connect TC4 to Nested Vector Interrupt Controller (NVIC)

  REG_TC4_INTFLAG |= TC_INTFLAG_OVF;              // Clear the interrupt flags
  REG_TC4_INTENSET = TC_INTENSET_OVF;             // Enable TC4 interrupts
  // REG_TC4_INTENCLR = TC_INTENCLR_OVF;          // Disable TC4 interrupts
 
  REG_TC4_CTRLA |= TC_CTRLA_PRESCALER_DIV256 |   // Set prescaler to 1024, 48MHz/1024 = 46.875kHz
                   TC_CTRLA_WAVEGEN_MFRQ |        // Put the timer TC4 into match frequency (MFRQ) mode 
                   TC_CTRLA_ENABLE;               // Enable TC4
  while (TC4->COUNT16.STATUS.bit.SYNCBUSY);       // Wait for synchronization
} 

void turnOffEncoders() {
  //analogWrite(ENC1_LED, 0);
  //analogWrite(ENC2_LED, 0);
  digitalWrite(ENC1_LED, LOW);
  digitalWrite(ENC2_LED, LOW);
}

void turnOnEncoders() {
  //analogWrite(ENC1_LED, 200);
  //analogWrite(ENC2_LED, 200);
  digitalWrite(ENC1_LED, HIGH);
  digitalWrite(ENC2_LED, HIGH);
}

void turnOffMotors(){
  
}

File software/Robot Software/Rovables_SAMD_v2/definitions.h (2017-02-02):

//Address of MPU
#define MPU_ADDRESS 0x68

//Pins
#define  LED_BLUE A3 
#define  LED_RED  A4
#define  CE       2  
#define  CSN      10
#define  INT_IMU  5
#define  M1_DIR   A2 
#define  M1_PWM   9 
#define  M2_PWM   4 
#define  M2_DIR   A1 
#define ENC1_INT  3  
#define ENC2_INT  7
#define ENC1_LED  8
#define ENC2_LED  6
#define TX_PIN    1
#define RX_PIN    0

//RF packet size
#define PACKET_SIZE 7

//OP codes commands
#define IGNORE    0x01
#define MOTOR_CRL 0x02

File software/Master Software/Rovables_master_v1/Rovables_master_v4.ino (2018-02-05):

#include <SPI.h>
#include "nRF24L01.h"
#include "RF24.h"

//Define pins
#define  LED_BLUE     A3 
#define  LED_RED      A4
#define  CE           10  
#define  CSN          9
#define BUTTON_X      A9
#define BUTTON_Y      A8
#define  DEBUG_PIN    0
#define MOTOR_OPCODE  0x02
#define POTENTIOMETER A4 


#define PACKET_SIZE     15
#define BUFFER_SIZE     30
#define NUMBER_OF_NODES 6

//#define JOYSTICK CONTROL 
#define COMPUTER CONTROL

RF24 radio(CE,CSN); // Default SPI speed is 4Mbit, but should work up to 10MBbit

// Radio pipe addresses for the 2 nodes to communicate.
const uint64_t pipes[] = {0x7878787878LL, 0xB3B4B5B6F1LL, 0xB3B4B5B6CDLL, 0xB3B4B5B6A3LL, 0xB3B4B5B60FLL, 0xB3B4B5B605LL };


bool SERIAL_DEBUG  = true;
uint8_t receiveData[PACKET_SIZE] = { };
uint8_t sendData[PACKET_SIZE] = { };

int state = 0;
int speed_forward  = 0;  

uint8_t robotUnderControl = 0;

uint8_t serialBuffer[BUFFER_SIZE] = { }; //Initialize to zeros
uint8_t computerReceiveBuffer[PACKET_SIZE][NUMBER_OF_NODES] = { };


void setup(void)
{

  pinMode(LED_BLUE, OUTPUT); 
 // pinMode(LED_RED, OUTPUT);
  pinMode(DEBUG_PIN, OUTPUT);
  pinMode(POTENTIOMETER, INPUT);

  SerialUSB.begin(0);

  radio.begin();

  radio.setRetries(10,0); //retries, delay
  radio.setPayloadSize(PACKET_SIZE);
  radio.setDataRate(RF24_2MBPS);
  radio.setChannel(60);

  radio.openReadingPipe(0,pipes[0]);
  radio.openReadingPipe(1,pipes[1]);
  radio.openReadingPipe(2,pipes[2]);
  radio.openReadingPipe(3,pipes[3]);
  radio.openReadingPipe(4,pipes[4]);
  radio.openReadingPipe(5,pipes[5]);

  radio.startListening();

  digitalWrite(LED_RED, HIGH); 
 
}

void loop(void)
{

  //Under joystick control. 
  getJoyStickData();
  
  //--------------CHECK FOR SERIAL PORT DATA---------------
  byte pipeNum = 0; //variable to hold which reading pipe sent data
  byte gotByte = 0; //used to store payload from transmit module
  int numBytes =0;
  while(Serial.available()) { 
    serialBuffer[numBytes] = SerialUSB.read();
    numBytes++;  
  }
  

  if (serialBuffer[0] == '@') { 
      int whereToSend = serialBuffer[1]*256; 
      whereToSend = whereToSend + serialBuffer[2];
      byte opCode = serialBuffer[3]; 
      byte sizeofData = serialBuffer[4]; 
      for (int i=1; i<sizeofData; i++) {
        computerReceiveBuffer[i][whereToSend] = serialBuffer[i+4]; 
      }//end for 
      computerReceiveBuffer[0][whereToSend] = opCode;

      for(int i=0; i<sizeof(serialBuffer); i++) serialBuffer[i] =0;

      //for(int i=0; i<PACKET_SIZE; i++) { 
      //  Serial.println(computerReceiveBuffer[i][whereToSend]);
      //}
      
  }
  
  //------------CHECK THE RADIO----------------------------
  while(radio.available(&pipeNum)){ //Check if received data
     digitalWrite(DEBUG_PIN,HIGH);
     radio.read( &receiveData, PACKET_SIZE ); //read one byte of data and store it in gotByte variable
     //printReceiveData(pipeNum);
     printReceiveDataFormated(pipeNum);
     delay(5);

      
     //Comment out below to enable joystick control
     #ifdef COMPUTER_CONTROL
     for(int i=0; i<PACKET_SIZE; i++) { 
      sendData[i] = computerReceiveBuffer[i][pipeNum];
     }
     #endif

     if (sendToSlave(pipeNum,  PACKET_SIZE)) {
        //Success sending   
     }
     else {
        //failed sending
     }
     digitalWrite(DEBUG_PIN,LOW);
  }//end while
}//end loop

bool sendToSlave(byte whichPipe, uint8_t packet_size) { 
     bool worked;   
     radio.stopListening(); 
     radio.openWritingPipe(pipes[whichPipe]); 
     if(!radio.write(&sendData,packet_size)) worked = false; 
     else worked = true; 
     radio.startListening(); 
     return worked; 
}//end sendToSlave

void printReceiveData(byte whichPipe) { 
   SerialUSB.print("S");
   SerialUSB.print(",");
   SerialUSB.print(whichPipe); 
   SerialUSB.print(",");
  for (int i=0; i<PACKET_SIZE; i++) {
         SerialUSB.print(receiveData[i]); 
         if(i<PACKET_SIZE-1){
          SerialUSB.print(",");
         }
  }
  SerialUSB.println(" ");
}

void printReceiveDataFormated(byte whichPipe) { 
   SerialUSB.print("S");
   SerialUSB.print(",");
   SerialUSB.print(whichPipe); 
   SerialUSB.print(",");
   SerialUSB.print(receiveData[0]); 
   SerialUSB.print(","); 
   SerialUSB.print(receiveData[1]); 
   SerialUSB.print(","); 
   SerialUSB.print(receiveData[2]); 
   SerialUSB.print(","); 

   unsigned long d;
    d =  (receiveData[6] << 24) | (receiveData[5] << 16) | (receiveData[4] << 8) | (receiveData[3]);
   float member = *(float *)&d;
   SerialUSB.print( member ); 
   SerialUSB.print(","); 

   d =  (receiveData[10] << 24) | (receiveData[9] << 16) | (receiveData[8] << 8) | (receiveData[7]);
   member = *(float *)&d;
   SerialUSB.print( member ); 

   SerialUSB.print(","); 

   d =  (receiveData[14] << 24) | (receiveData[13] << 16) | (receiveData[12] << 8) | (receiveData[11]);
   member = *(float *)&d;
   SerialUSB.println( member ); 

}

void getJoyStickData() { 
  int forward_back = analogRead(BUTTON_X); 
  int left_right = analogRead(BUTTON_Y); 
  float speed_scalar = (float)analogRead(POTENTIOMETER)/594.0;
  speed_forward  = 0;  
  int intesityTurn = 0; 
  if (forward_back>=556) { 
    speed_forward = speed_scalar*((forward_back-556)/2);
    
  }
  else if (forward_back<556) {
     speed_forward = speed_scalar*((556-forward_back)/2)-25;
     if(speed_forward <=0)  speed_forward = 0;
  }

  //debugButtons();

  if (left_right >700) { 
    //turn LEFT
      sendData[0] = MOTOR_OPCODE;
      sendData[1] = 120; 
      sendData[2] = 120;
      sendData[3] = 1;
      sendData[4] = 1;
      state = 1; 
  }

  else if (left_right < 300) { 
    //turn RIGHT
      sendData[0] = MOTOR_OPCODE;
      sendData[1] = 130; 
      sendData[2] = 130;
      sendData[3] = 0;
      sendData[4] = 0;
      state =2;
  }

  else if (forward_back > 600) { 
    //go FORWARD 
      sendData[0] = MOTOR_OPCODE;
      sendData[1] = speed_forward; 
      sendData[2] = speed_forward; 
      sendData[3] = 1;
      sendData[4] = 0;
      state = 3; 
  }

  else if (forward_back < 400) {
    //go BACKWARDS
      sendData[0] = MOTOR_OPCODE;
      sendData[1] = speed_forward;  //turning left  60/60 original
      sendData[2] = speed_forward;
      sendData[3] = 0;
      sendData[4] = 1;
      state = 4;
  }

  else  { 
    sendData[0] = MOTOR_OPCODE;
    sendData[1] = 0; 
    sendData[2] = 0;
    state = 0;
  }
}

void debugButtons() { 
  SerialUSB.print(analogRead(BUTTON_X));
  SerialUSB.print(",");
  SerialUSB.print(analogRead(BUTTON_Y));
  SerialUSB.print(","); 
  SerialUSB.print(state);
  SerialUSB.print(",");
  SerialUSB.println(speed_forward); 
}

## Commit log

2017-02-02 more stuff
    [BOM_assembly.xlsx, PCB_Flex_cable_Encoder.PcbDoc, PCB_IR_Encoder_v2.PcbDoc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]
2017-02-02 added CAD file
2017-02-02 added joystick cad
2017-02-19 Added new robot software
    fixed:
    1) bug with counter
    2) Channel frequency to 60
    3) Added sleep code between radio transmissions.
    4) Removed the sleep line in write for NRF24 library
    [Rovables_SAMD_v2.ino, definitions.h]
2017-02-19 added IR assembly guide
2018-07-06 added 3d printing files
    [BB_Mg Adapter V2.STL, Magnet Holder V1C.STL, Mt_Mg Adapter V2.STL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]
2019-11-12 added about the SPI ports
